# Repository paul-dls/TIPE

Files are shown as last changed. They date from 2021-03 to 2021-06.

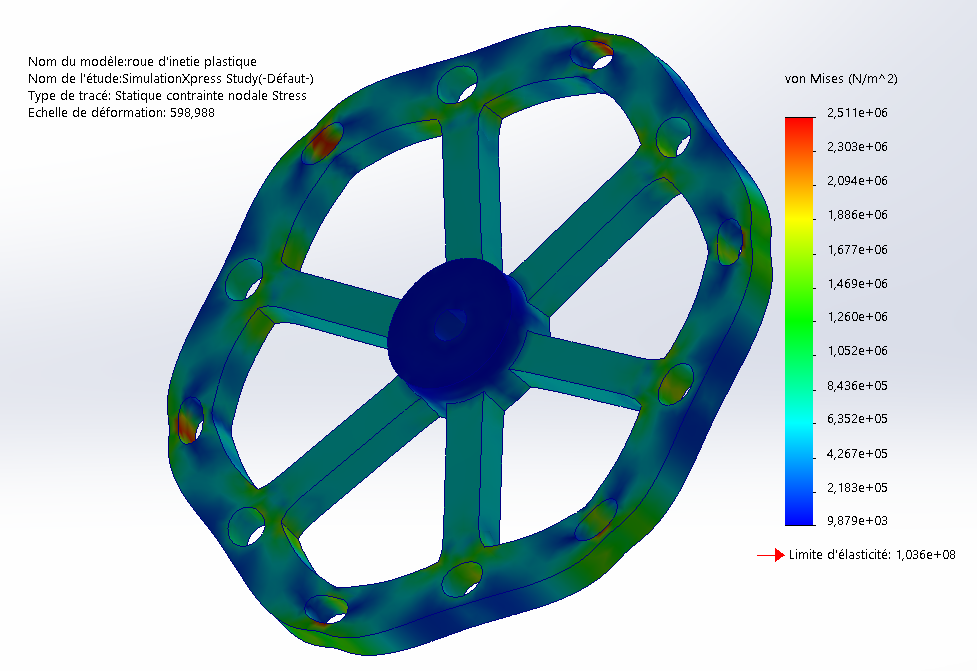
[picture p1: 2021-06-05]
photos/déformation du volant.PNG

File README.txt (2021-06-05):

ceci est un TIPE sur le contrôle de l'orientation des satellites
le concept est d'utiliser un volant d'inertie pour entrainer une rotation du sattelite par conservation du moment cinetique,
pour cela on place le 'satellite' de test sur un pivot et on ne s'nteresse qu'à la rotation selon l'axe vertical
Ce système est appelé un CMG(control moment gyro), on a un volant d'inertie qui tourne à vitesse constante dont on fait varier l'oriention ce qui permet le contrôle

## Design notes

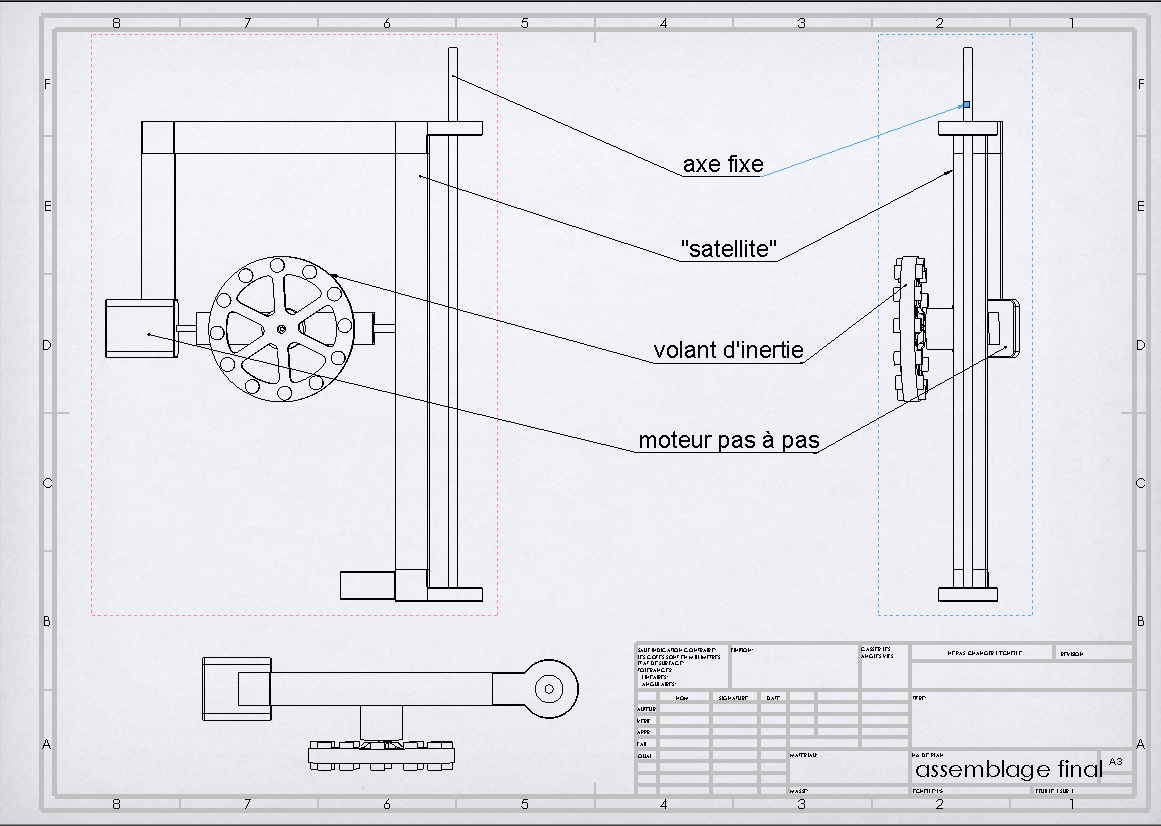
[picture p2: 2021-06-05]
photos/plan final 2 .PNG

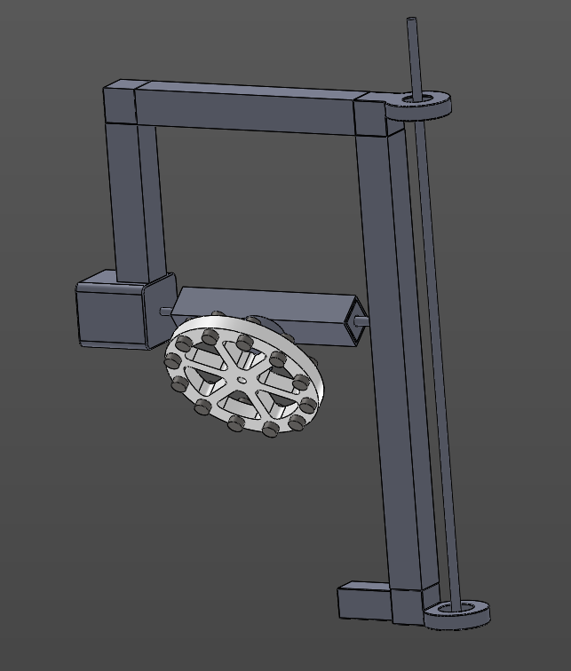
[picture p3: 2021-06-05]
photos/plan final.PNG

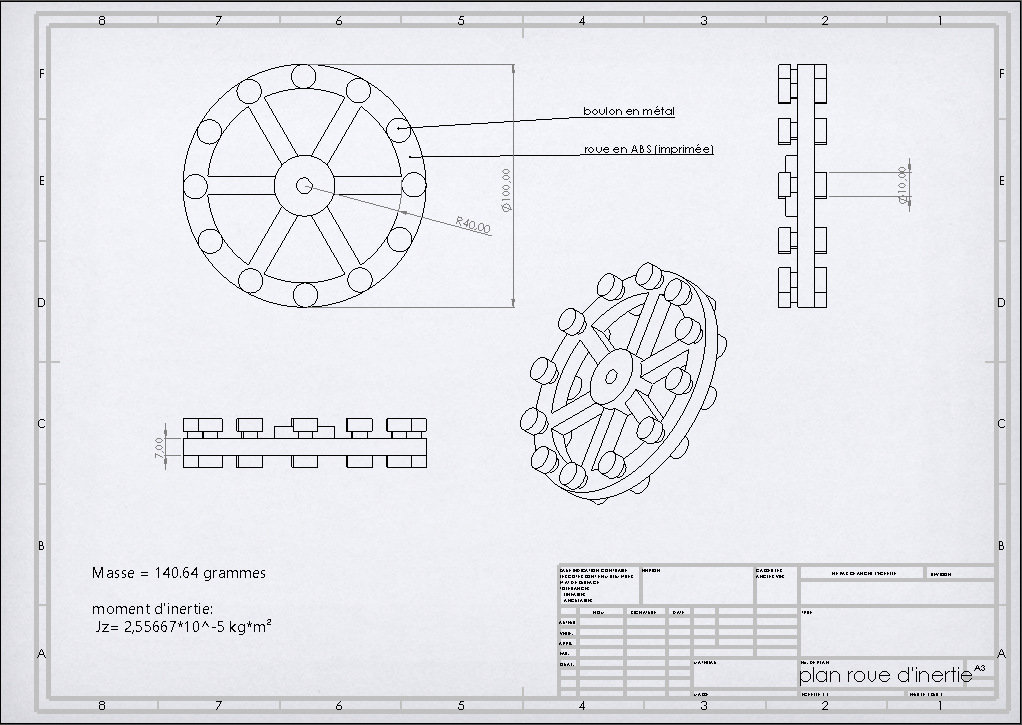
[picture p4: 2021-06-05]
photos/ancienne roue d'inertie.PNG

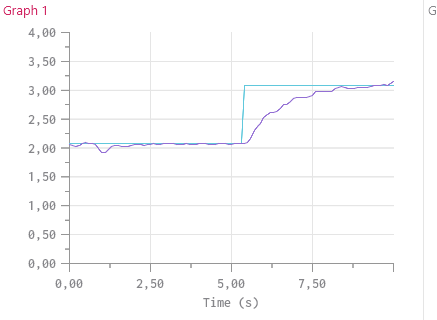
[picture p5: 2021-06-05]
courbes/K = 3, a= 25, Td=45.PNG

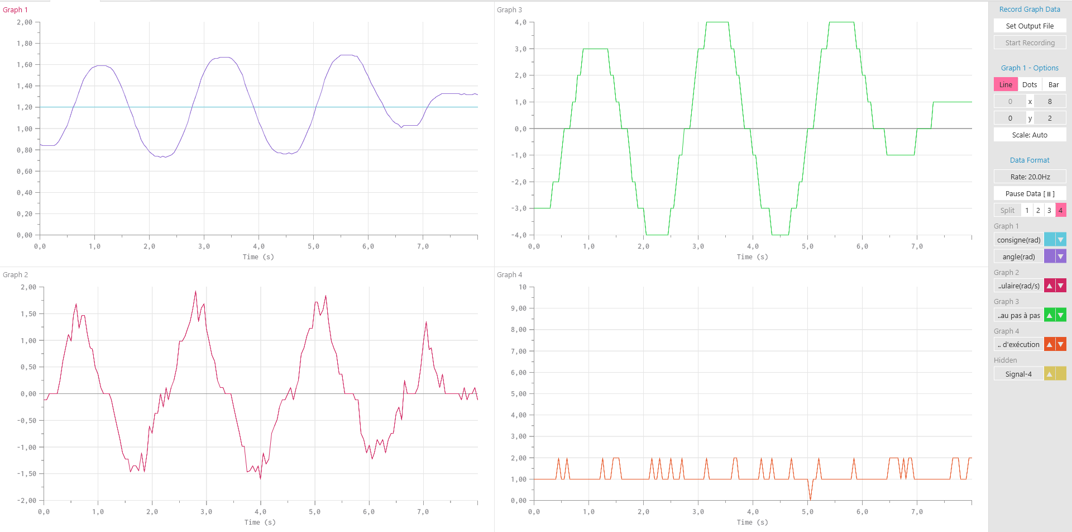
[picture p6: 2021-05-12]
courbes/KP trop grand.PNG

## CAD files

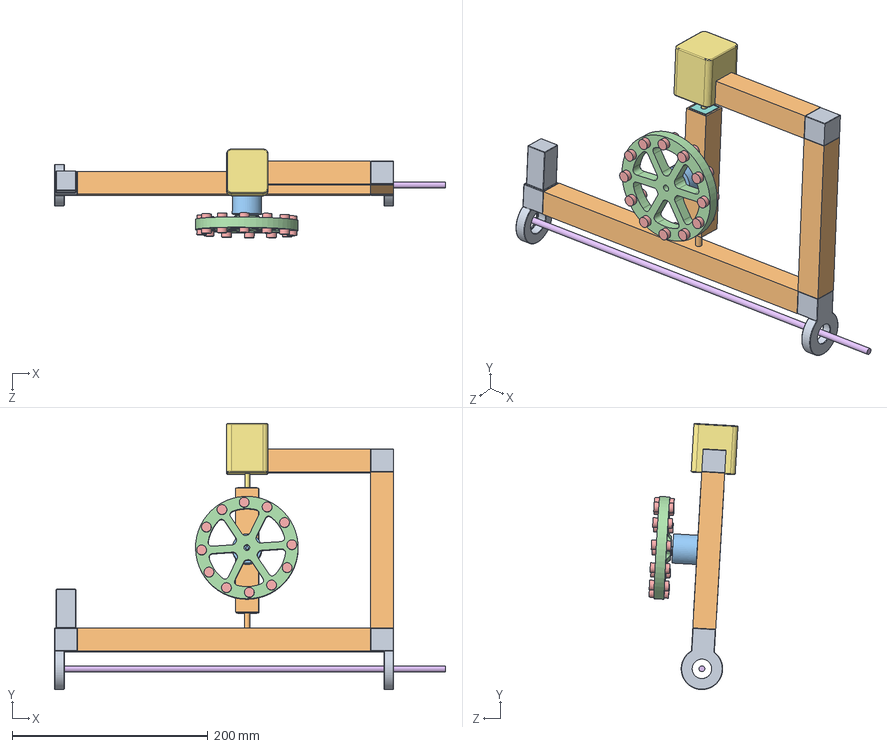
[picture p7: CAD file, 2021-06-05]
pieces solidworks/assemblage final.SLDASM
400.0 x 272.3 x 91.1 mm
coin x 3
tube x 4
motor
roue d'inetie plastique
vis x 12
axe central
pasAPas
axe moteur pas a pas
trou pour bvis
vis support

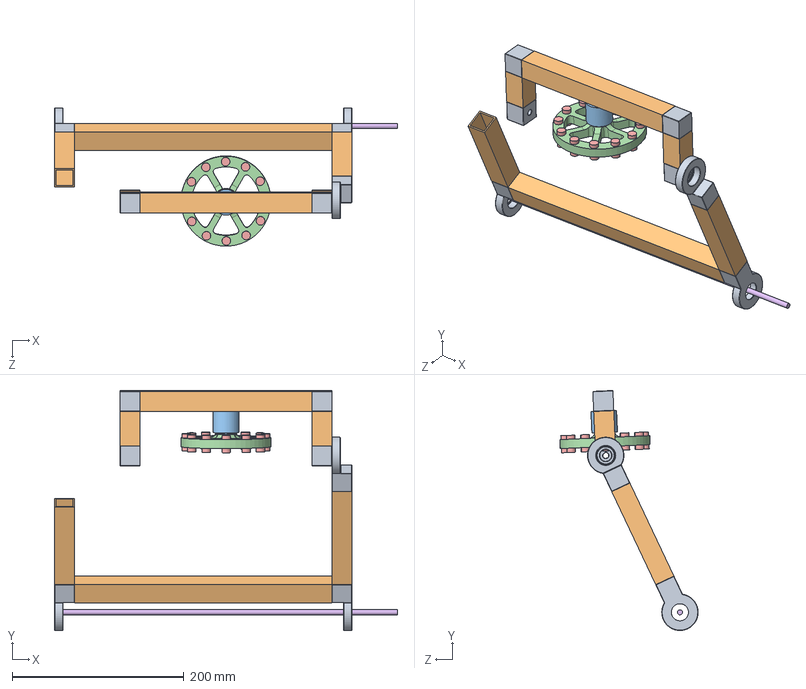
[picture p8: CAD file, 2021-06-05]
pieces solidworks/TIPE2.SLDASM
400.0 x 279.9 x 161.3 mm
coin x 7
tube x 6
motor
roue d'inetie plastique
vis x 12
axe central

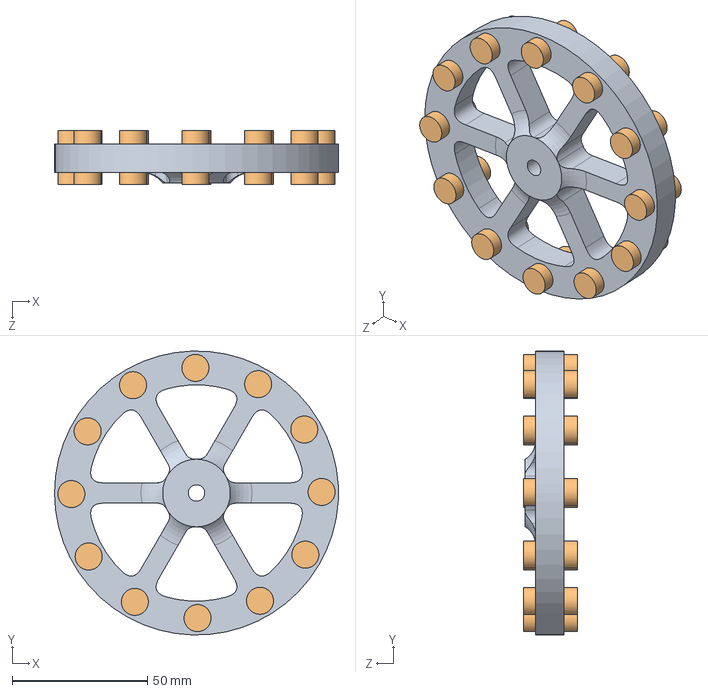
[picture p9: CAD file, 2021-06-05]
pieces solidworks/roue d'inertie.SLDASM
105.0 x 105.0 x 20.0 mm
roue d'inetie plastique
vis x 12

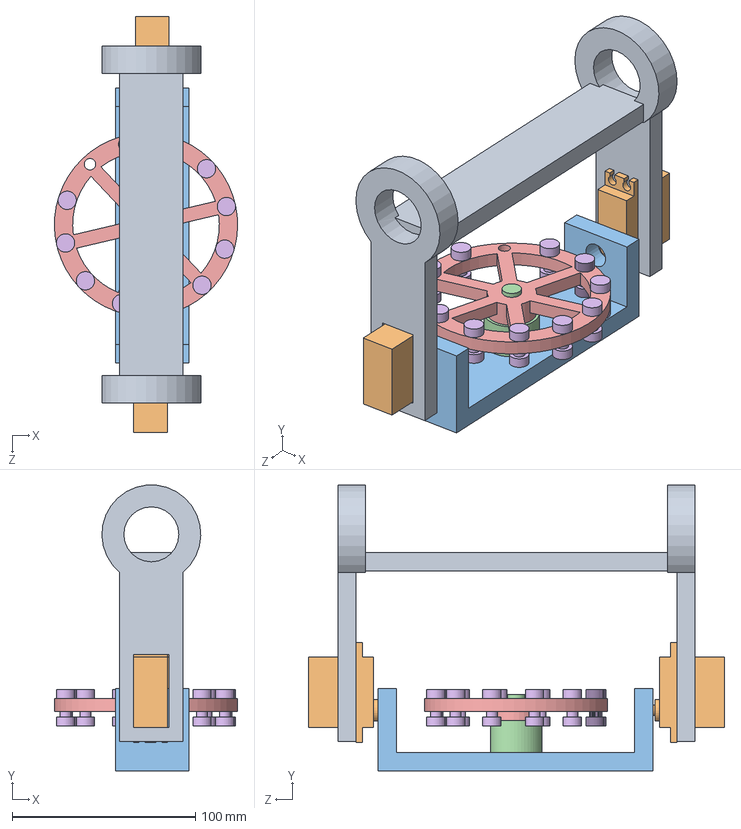
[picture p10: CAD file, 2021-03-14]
pieces solidworks/assemblageTipe.SLDASM
100.0 x 155.9 x 227.0 mm
exterieur
grandServo x 2
ensembleRotation
moteur
roue d'inetie plastique
vis x 12

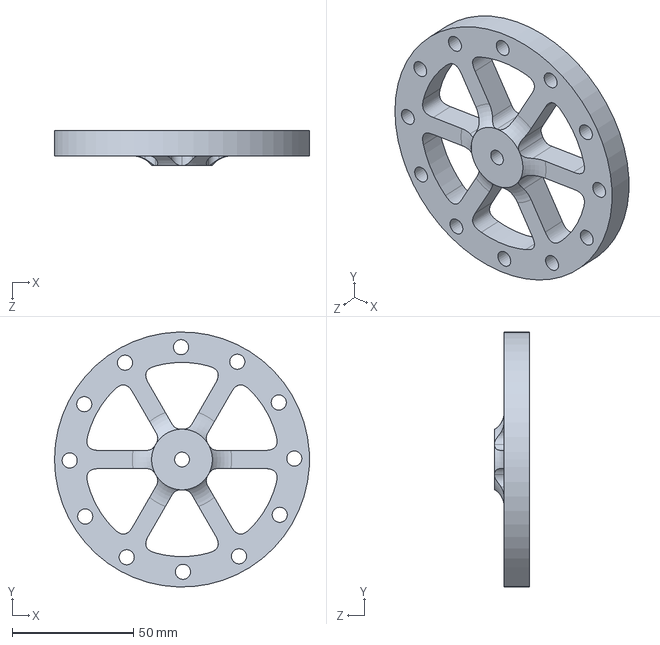
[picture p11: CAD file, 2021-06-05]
pieces solidworks/roue d'inetie plastique.SLDPRT
105.0 x 105.0 x 14.5 mm

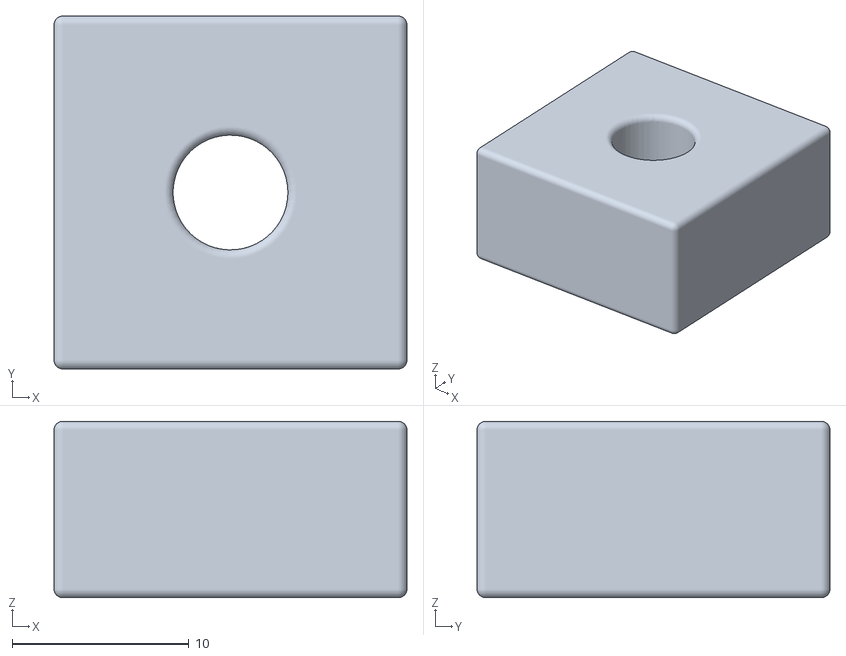
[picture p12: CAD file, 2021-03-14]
pieces solidworks/STL/axe vis.STL
20.0 x 20.0 x 10.0

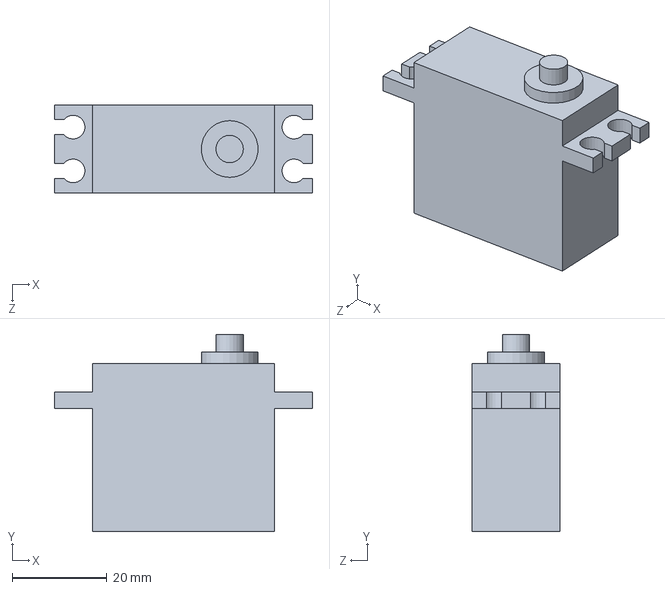
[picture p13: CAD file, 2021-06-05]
pieces solidworks/grandServo.SLDPRT
54.5 x 41.7 x 18.5 mm

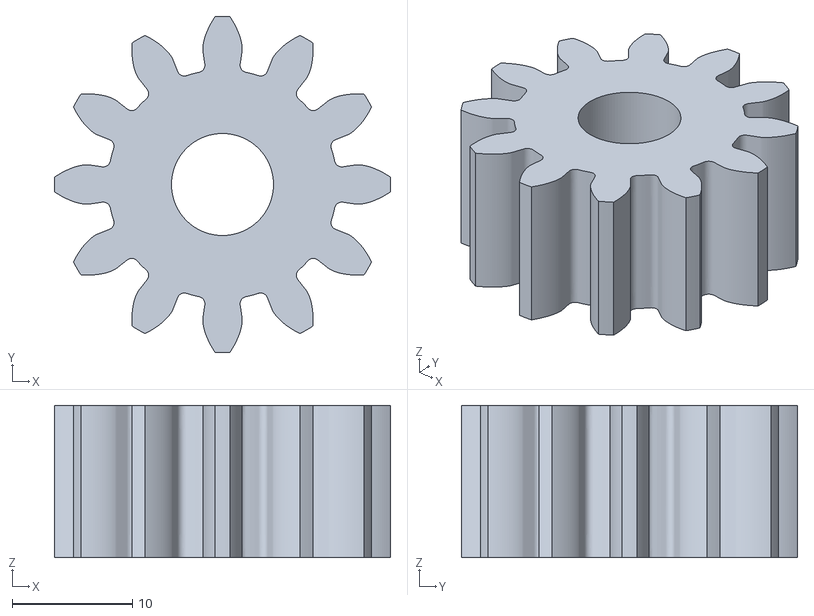
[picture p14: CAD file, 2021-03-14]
pieces solidworks/STL/engrenage axe.stl
28.0 x 28.0 x 12.7

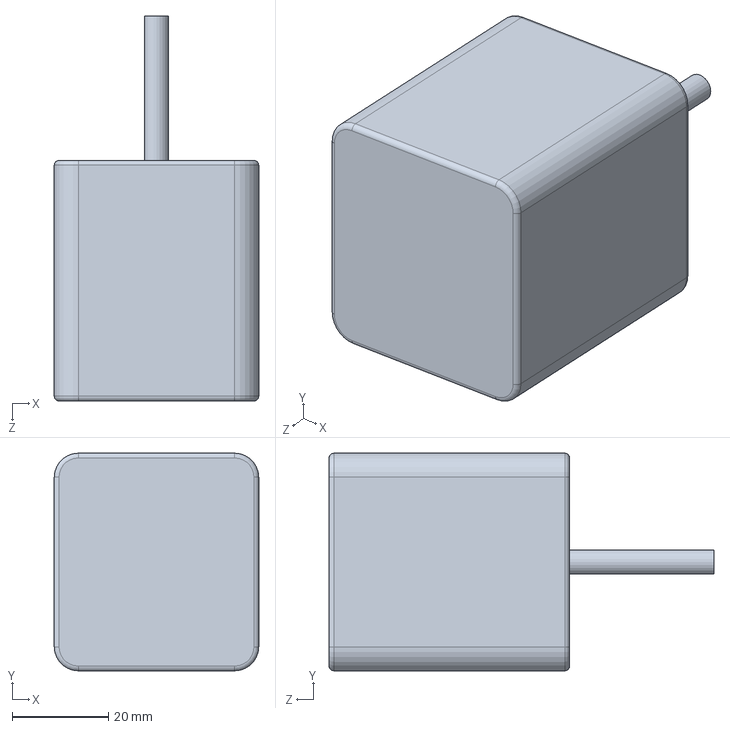
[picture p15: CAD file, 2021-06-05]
pieces solidworks/pasAPas.SLDPRT
42.5 x 45.2 x 80.0 mm

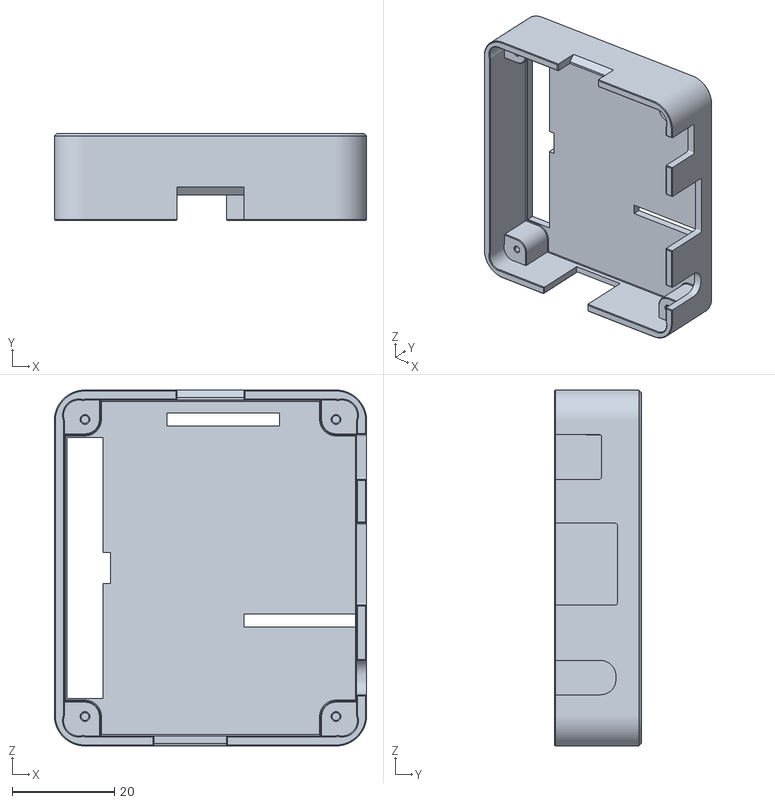
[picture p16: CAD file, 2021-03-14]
pieces solidworks/STL/top_noGrid_AllSlots_r1.STL
61.0 x 17.0 x 69.5

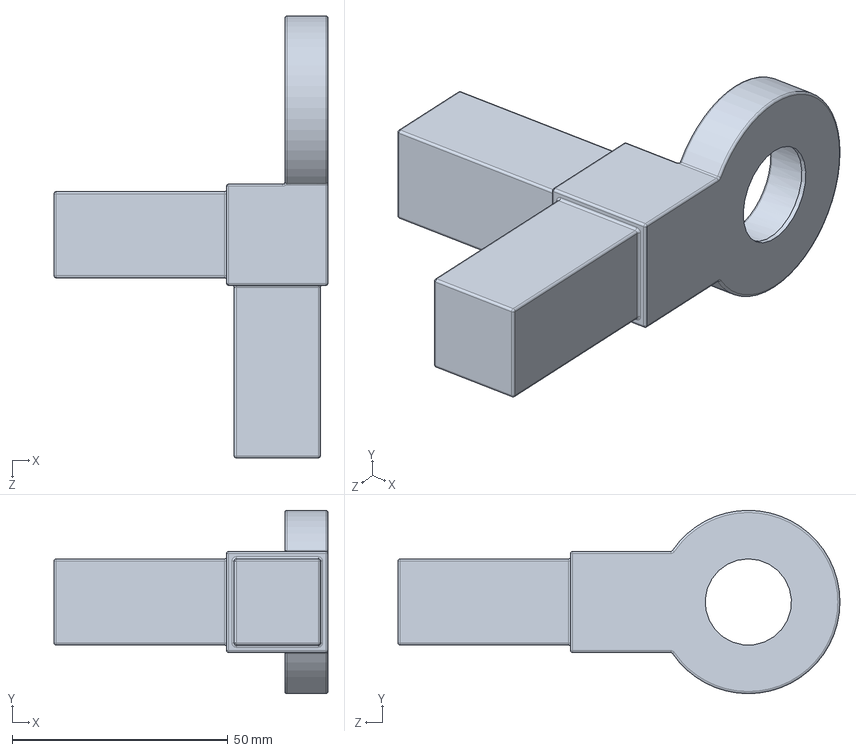
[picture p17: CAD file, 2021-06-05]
pieces solidworks/coin.SLDPRT
63.5 x 42.5 x 102.5 mm

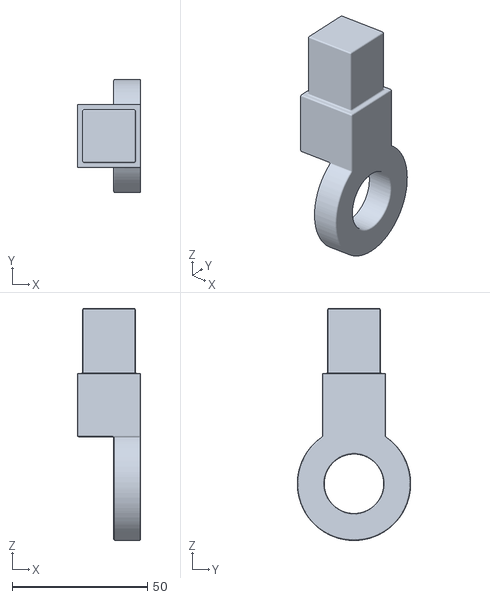
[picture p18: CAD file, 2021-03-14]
pieces solidworks/STL/ligne.STL
23.5 x 42.0 x 85.9

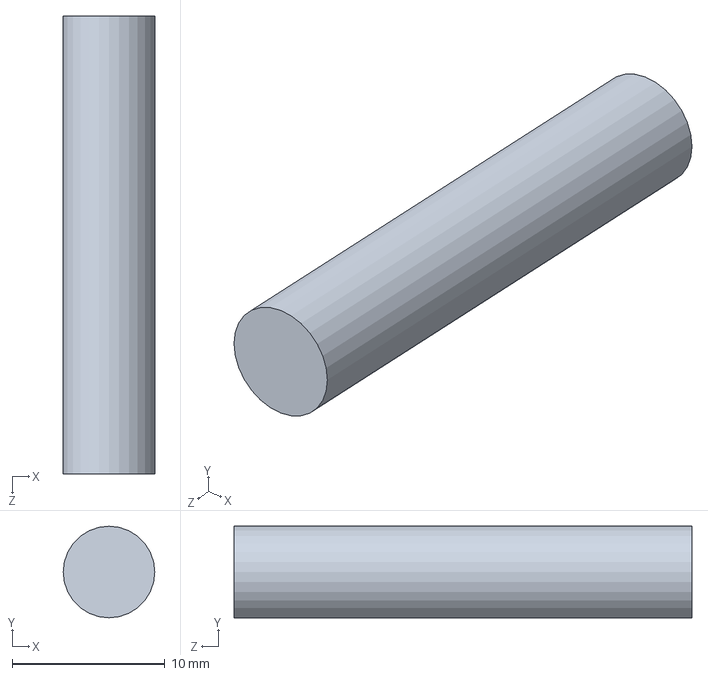
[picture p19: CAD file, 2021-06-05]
pieces solidworks/vis support.SLDPRT
6.00 x 6.00 x 30.0 mm

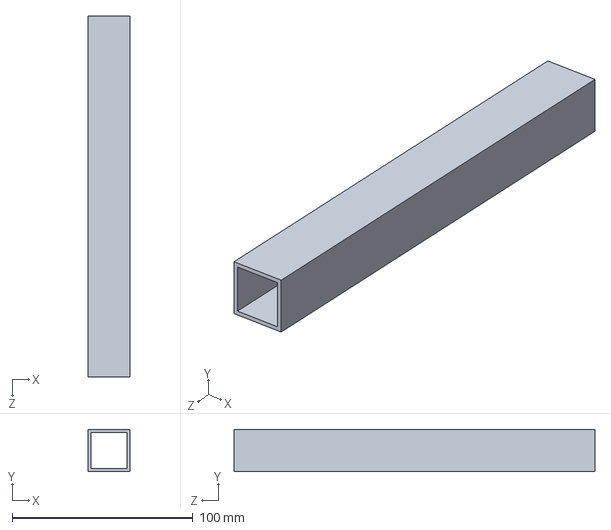
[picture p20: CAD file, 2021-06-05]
pieces solidworks/tube.SLDPRT
23.5 x 23.5 x 200.0 mm

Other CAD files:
pieces solidworks/STL/engrenage potentiometre.stl
pieces solidworks/vis.SLDPRT
pieces solidworks/exterieur.SLDPRT
pieces solidworks/motor mount.SLDPRT
pieces solidworks/STL/axe moteur pas a pas.STL
pieces solidworks/STL/coin.STL
pieces solidworks/STL/roue d'inetie plastique.STL
pieces solidworks/STL/support moteur.STL
pieces solidworks/axe central.SLDPRT
pieces solidworks/axe moteur pas a pas.SLDPRT
pieces solidworks/ensembleRotation.SLDPRT
pieces solidworks/mises en plan/assemblage final.SLDDRW
pieces solidworks/mises en plan/pauldlsTIPE.SLDDRW
pieces solidworks/mises en plan/plan roue d'inertie.SLDDRW
pieces solidworks/moteur.SLDPRT
pieces solidworks/motor.SLDPRT
pieces solidworks/support moteur.SLDPRT
pieces solidworks/trou pour bvis.SLDPRT

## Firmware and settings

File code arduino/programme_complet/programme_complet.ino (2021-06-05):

/*
 * Ce programme permet de controler l'orientation d'un solide sur un pivot vertical à partir d'un volant d'inertie 
 *  
 * le pas à pas est sur les pins 8 a 11
 * 
 * ce programme reprend des parties des exemples de la librairie Stepper
 * 
 * créé le 6 mars 2021
 * par Paul de La Sayette
 */
//librairies
#include <Servo.h>
#include <Stepper.h>

// pins
#define POT_PIN A0
#define pinMot 6

//constantes
#define pi 3.1416
#define stepsPerRevolution 200
#define processingOn true
#define tempsRafraichissement 100 //en ms

// constantes du correcteur
#define K 1.1
#define Td 45 //en ms
#define a 25

// variables golbales
float mesure; // en radian
float mesureOld = 0;// en radian
long int tempsOld = millis();//en ms
float deriv = 0; //en rad/s
long int derniereCom= millis();//en ms

float commande = 0; // en radian
float output; // en rad/s
int  motorSpeed=0;// en rpm

//objets
Servo moteur;
Stepper myStepper(stepsPerRevolution, 8, 9, 10, 11);


void setup() {
  Serial.begin(115200); // on définit un débit rapide pour ne pas ralentir l'arduino inutilement
  //while (!Serial) {}
  Serial.println("initialisation du port série");
  
  moteur.attach(pinMot,100,200);
  myStepper.setSpeed(10);
  delay(500);

  //initialisation du moteur
  moteur.write(125); 
  // on place l'ESC a 0 pour enlever la securité, j'utilise un esc de voiture télécommandé
  //son 0 n'est donc en réalité pas à 100 (borne basse du PWM) mais à 120
  for(int i=125; i<140 ; i++){ 
    // 120 correspond donc à 25% de la vitesse maximale, on est donc environ à 2500 tr/min(vérifié au stroboscope)
    moteur.write(i);
    Serial.println(i);
    delay(50);
  }
  delay(500);
  Serial.println("moteur lancé");

  commande = float(analogRead(POT_PIN))/1023*2*pi;
  Serial.println("commande :" + String(commande));
}

void loop() {
  //calcul de motorSpeed par un correcteur PD/avance de phase
  mesure = float(analogRead(POT_PIN))/1023*2*pi;
  deriv = ((mesure - mesureOld)/(millis()-tempsOld)+deriv)/2;// on fait une moyenne glissante sur 2 points

  //stockage des anciennes mesures
  mesureOld = mesure;
  tempsOld = millis(); 
  
  output = K *((mesure-commande) + Td*a*deriv);
  motorSpeed = output/(2*pi)*60;//output est en radian par seconde, motorspeed en rpm
  setMotorSpeed();

  //on impose une durée de boucle minimum ce qui filtre les hautes fréquences
  while(millis()-tempsOld < Td){
    delay(1);
  }

  //on communique avec l'ordinateur tout les 100ms 
  if (millis() - derniereCom >= tempsRafraichissement){
    com();
    derniereCom = millis();
  }
}
void com(){
  //communication avec l'ordinateur, j'utilise une synthaxe spaciale lorsque je fais des graphiques avec processing
  if (not processingOn ){
    Serial.print ("temps :" +String(millis()) + ", ");
    Serial.print ("mesure:" +String(mesure) + ", ");
    Serial.print("deriv:" + String(1000*deriv)+",");
    Serial.print ("commande :" +String(commande) + ", ");
    Serial.print ("output:" +String(output) + ", ");
    Serial.println ("motorSpeed:" +String(motorSpeed) );
  }
  else {
    Serial.print (String(commande) + ",");
    Serial.print (String(mesure)+",");
    Serial.print (String(1000*deriv)+",");
    Serial.print (String(motorSpeed)+ "," );
    Serial.println (String(millis()-tempsOld));
  }

  //l'ordinateur envoie "1" si il souhaite un échelon de 1 rad
  if (Serial.available() > 0) {
    if (Serial.read() == 49){ // 1 coorespond à 49 en ASCII
      commande = commande + 1;
    }
  }
}

void setMotorSpeed(){
  //on met a jour la vitesse du moteur et on lui fait se déplacer d'un pas
  if (motorSpeed > 60){//saturation haute
    myStepper.setSpeed(60);
    myStepper.step(1);
  }
  else if (motorSpeed > 0){//sens positif
    myStepper.setSpeed(motorSpeed+2);
    myStepper.step(1);
  }
  else if (motorSpeed < -60){//saturation basse
    myStepper.setSpeed(60);
    myStepper.step(-1);
  }
  else if (motorSpeed < 0) {//sens négatif
    myStepper.setSpeed(- motorSpeed+2);
    myStepper.step(-1);
  }
}

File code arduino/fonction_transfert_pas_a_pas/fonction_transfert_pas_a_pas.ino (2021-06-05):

/*
 Stepper Motor Control - one revolution

 This program drives a unipolar or bipolar stepper motor.
 The motor is attached to digital pins 8 - 11 of the Arduino.

 The motor should revolve one revolution in one direction, then
 one revolution in the other direction.


 Created 11 Mar. 2007
 Modified 30 Nov. 2009
 by Tom Igoe

 */

#include <Stepper.h>

const int stepsPerRevolution = 200;  // change this to fit the number of steps per revolution
// for your motor

// initialize the stepper library on pins 8 through 11:
Stepper myStepper(stepsPerRevolution, 8, 9, 10, 11);

void setup() {
  // set the speed at 60 rpm:
  myStepper.setSpeed(20);
  // initialize the serial port:
  Serial.begin(9600);
  pinMode(13,OUTPUT);

  delay(2000);
  digitalWrite(13,HIGH);
  delay(500);
  digitalWrite(13,LOW);
  myStepper.step(50);
  delay(4000);
  
}

void loop() {
  // step one revolution  in one direction:
  delay(100);


  

}

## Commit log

2021-03-14 ajout des fichiers 3D
    touts les fichiers 3D sur solidworks 2020
    [axe central.SLDPRT, axe moteur pas a pas.SLDPRT, axe moteur pas a pas.STL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]
2021-03-14 ajout des codes arduino en desorde
    [TIPE2.SLDASM, assemblageTipe.SLDASM, pauldlsTIPE.SLDDRW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]
2021-05-12 premières mesures et amelioration du code
    [correscteur P avec KP trop grand.csv]
2021-06-05 améliorations finales
    choix des constantes du correcteur,
    ajout de photos et de courbes
    amélioration du code
    [TIPE2.SLDASM, assemblage final.SLDASM, assemblage final.SLDDRW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]
